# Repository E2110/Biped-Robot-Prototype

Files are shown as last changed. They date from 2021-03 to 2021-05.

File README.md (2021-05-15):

# Biped-Robot-Prototype

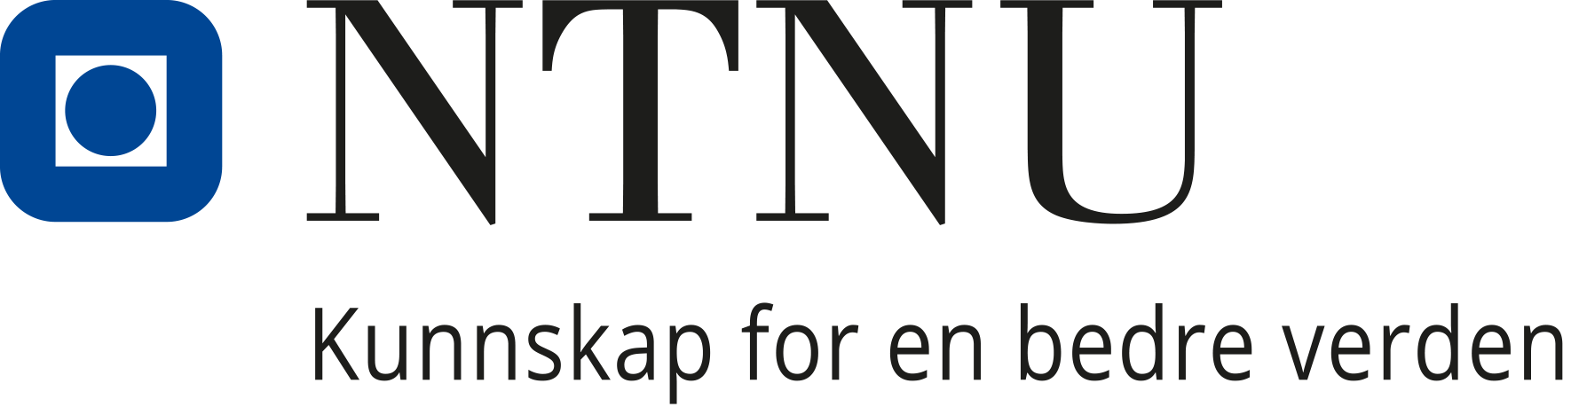
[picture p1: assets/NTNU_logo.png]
NTNU_logo


This is the reposatory for our Bachelor's thesis. The target group for this git is other electrical engeneering students at NTNU. Therefor knowledge acquired during the course of study is to be expected. The documentaions and explanaitons in this git should give enough information to be a foundation for further work. 

Anyways this project is about a thin and simple robot that can't walk. We will teach it to walk. How? Through C++ and ROS. Each part of the robot will have it's own floder where we explain the code and everything? associated with that part. 

https://user-images.githubusercontent.com/78819338/118373048-e83d3c00-b5b4-11eb-93af-3f74fb1a81d0.mp4

# Flashing Ubuntu 18.04
From windows OS. For flashing the new image we used following:

* Micro-SD, 16 GB
* 7-zip
* balenaEtcher

1 . Download prebuilt image from https://elinux.org/BeagleBoardUbuntu. As of writing the direct link to the image is https://rcn-ee.com/rootfs/2020-03-12/flasher/bone-eMMC-flasher-ubuntu-18.04.4-console-armhf-2020-03-12-2gb.img.xz and the downloaded file is called.

```
 bone-eMMC-flasher-ubuntu-18.04.4-console-armhf-2020-03-12-2gb.img.xz
```
2. Extract the file using 7-zip. This will remove the .xz at the end of the file.

3. Insert the Micro-SD into the computer. Open balenaEtcher, select flash from file and pick the the newly extracted .img file. Select the Micro-SD as target. FLASH!

4. Remove the Micro-SD from computer and insert it into the Beaglebone.

5. Hold the S3-botton down while powering up the Beaglebone. Hold until the four lights left of the ethernet input lights up at the same time, then let go of the button. The Beaglebone will then boot for quite some time until its done.

# Connect to the BeagleBone through SSH.

```
ssh ubuntu@192.168.7.2
```
passord: temppwd

# Enable the PWM-pins
This depends on your device tree overlay. There are quite a bunch out there, this one follows the one we got from the flashed image above.

1. Change to root user.

```
sudo su
```
2. Go to the ocp folder for the pin you want use. In this example P9_16.

```
cd /sys/devices/platform/ocp/ocp:P9_16_pinmux
```

3. Use cat state to see what pin-mode is currently in use. Use echo to change to PWM.

```
echo pwm > state
```

# Write to the PWM-pins with terminal

After changing the state to PWM you can change the different PWM-values in /sys/class/pwm/-folder. This is done by echoing different values to the parameters you want to change. In the example under we do this to pin P9.14

```
cd /sys/class/pwm/pwm-4:0
```
The three parameters we care about:
* enable: Turn on and of the pin.
* period: Decides the frequency. 
* duty_cycle: Time high during the period. If you put it the same as the period it will be constant high.

```
echo 1000000 > period
echo 200000 > duty_cycle
echo 1 > enable
```

# Write to the GPIO-pins with terminal
Go to the GPIO-folder
```
cd /sys/class/gpio
```
With the current Device Three Overlay the ls commando will show us a lot of gpio-pins to begin with. Even though only the current exported gpios should show up, we noticed that a lot of the pins were not exported. So if you can't change the paramters of a certain pin, we recommend trying to unexport and export that pin. This is done by echoing the number of the gpio to the unexport and export.

```
echo 114 > unexport
echo 114 > unexport
```
Now cd into the gpio you want to change.

```
cd gpio115
```
The two paramteres you should care about:
* direction: either in or out
* value: 1 or 0

# Install ROS-melodic

http://wiki.ros.org/melodic/Installation/Ubuntu

# Transfering files to the BeagleBone
## Linux
To do this we use scp command in the terminal

```
scp localfile.cpp ubuntu@192.168.7.2:/folder
```
Eclipse is also a common tool you can use for this and cross compiling.

## Windows
To transfer from windows we use WinSCP. Its pretty straight forward to use, kind of like a windows version of eclipse. 

1. Go to https://winscp.net/eng/download.php and install Winscp.

2. Connect the Beaglebone to your computer and open Winscp. This should pop up.

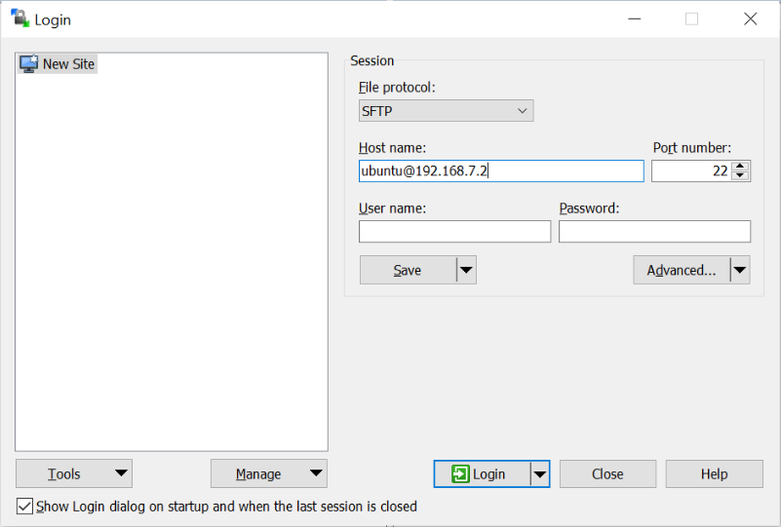
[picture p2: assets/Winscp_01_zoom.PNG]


3.Write ubuntu@192.168.7.2 into Host name. Port Number should stay at 22.

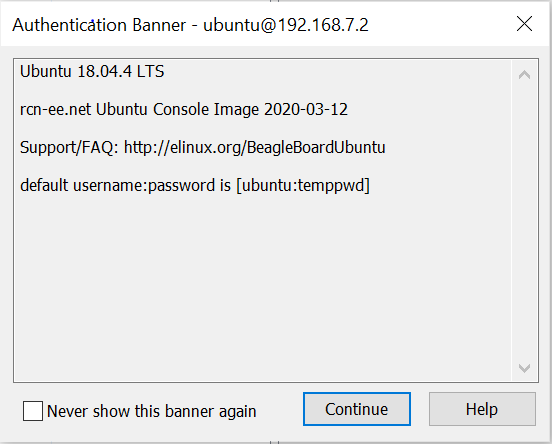
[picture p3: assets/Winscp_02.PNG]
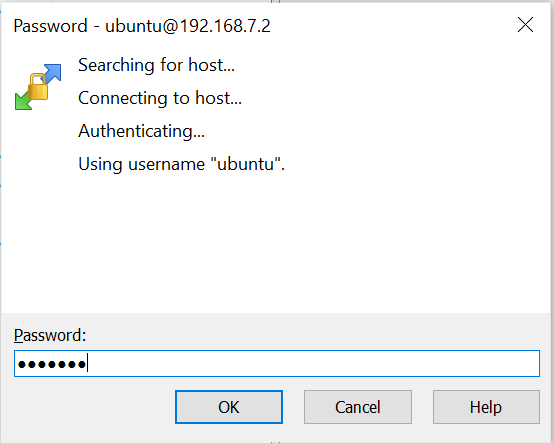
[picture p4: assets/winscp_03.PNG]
|

4. When connected you can easily drag end drop between the Beaglebone and the pc. You can also edit the different files on beaglebone.

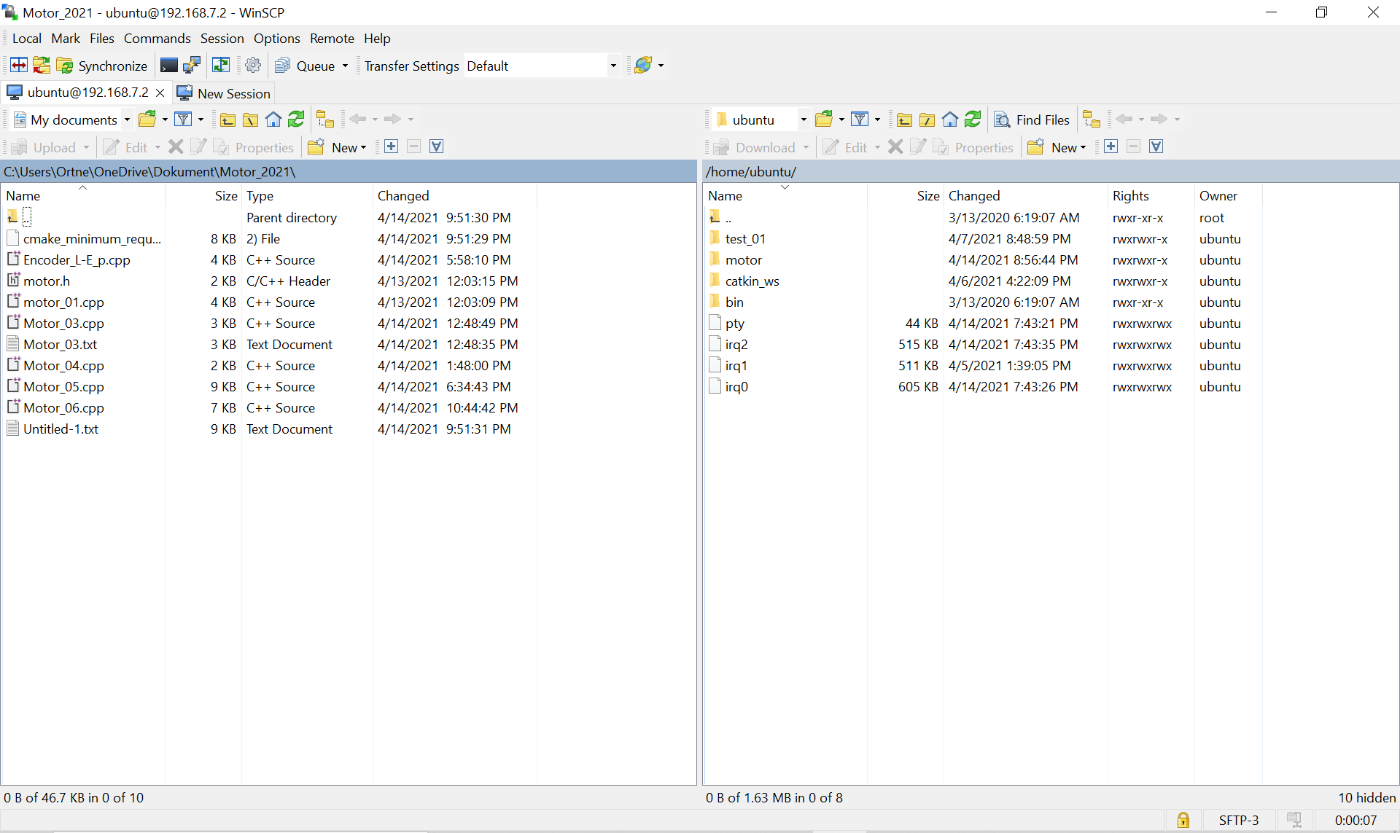
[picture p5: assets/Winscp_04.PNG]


# Make a Catkin-workspace, compile and run a C++-file with ROS
<i> This should be failry simple if you have gone through the ROS-tutorials. We'll keep it as short as possible.</i> 

1. Open one terminal (Ctrl + Alt + T) and run roscore

```
roscore
```
2. Open another (Ctrl + Shift + T) and source setup.bash

```
source /opt/ros/melodic/setup.bash
```
3. Make a folder and another named "src" within this one.

```
mkdir folder_01
cd folder_01
mkdir src
```
4. Make Cmakelists.txt vha. catkin_init_workspace

```
cd src
catkin_init_workspace
```
5. Exit src and run catkin_make

```
cd ..
catkin_make
```
6. source setup.bash

```
source devel/setup.bash
```

7. Make package

```
cd src
catkin_create_pkg folder_02 roscpp std_msgs
```
8. Import C++-file to new src folder.
9. To be able to run a C++-file you have to edit CMakelists.txt in folder_02

```
nano CMakeLists.txt
```
Under "Build"-section you can uncomment the "add_executable", "add_dependencies" and "target_link_libraries". Optionally just add:

```
add_executable(number_3 src/C++-file.cpp)
add_dependencies(number_3 ${${PROJECT_NAME}_EXPORTED_TARGETS} ${catkin_EXPORTED_TARGETS})
target_link_libraries(number_3 ${catkin_LIBRARIES})
```
10. Go to folder_01 and run catkin_make. This should compile the package.
```
cd ../..
catkin_make
```
11.Run the package
```
rosrun number_3 folder_02
```

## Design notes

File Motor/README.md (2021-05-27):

# Motor

The motors are located at the joint between torso and legs. By manipulating the ratio between period and duty-cycle we can decied the current delivered to the motors and by changing the value of the GPIO-pins we can change the directions of the motors. In the robots embeded system this part consists of three parts:

Maxon Motor 14887            |   ESCON 70/10 Servocontroller    |   Gearhead GP42C
:------------------------------------:|:-------------------------------------:|:-------------------------:
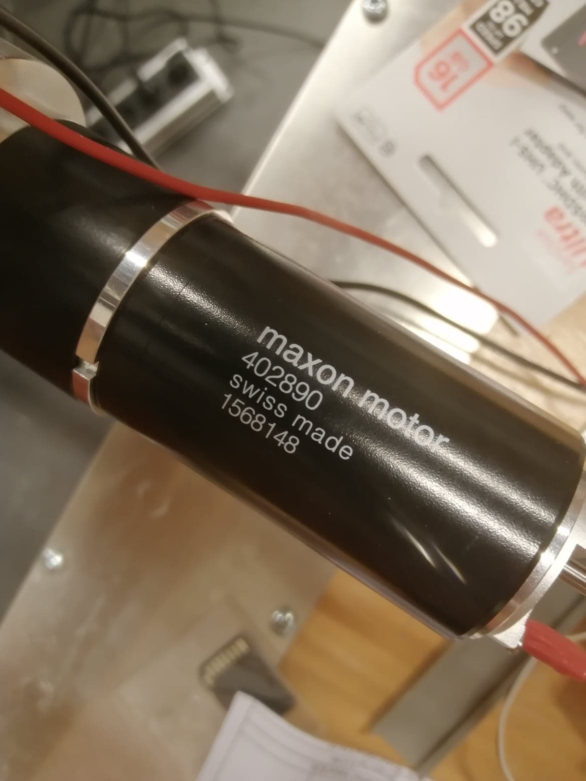
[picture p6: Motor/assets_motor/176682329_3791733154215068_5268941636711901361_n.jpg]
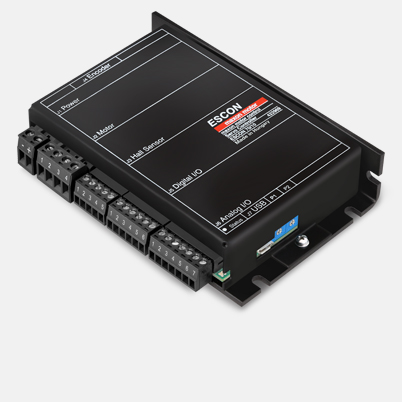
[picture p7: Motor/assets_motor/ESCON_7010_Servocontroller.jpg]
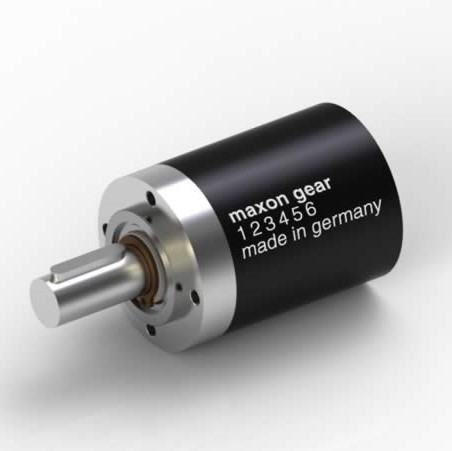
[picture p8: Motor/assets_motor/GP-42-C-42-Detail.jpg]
  |   | 

NB. The part number written on the motor (402890) is the part number for the particular motor/gearhead combination. We also have a spare with the number 241318. This consists of the same motor, but different gearhead. The spare gearhead has a ratio of 1:26.

The implemented gearheads have ratios of 1:6. 

Before the code for the motor is run its important to configure the servo controller with the ESCON studio software. Work done by a prior bachelor thesis group determined that the maximum required amperage for the motor should be 8.3A, this should be configured with the ESCON software including preforming a autotuning.

## Configure the servo-controller
To configure the ESCON 70/10 Servocontroller you need:
* Escon studio (Software)
* Micro USB
* Power Supply (If you want to Auto tune it)
The config is quite simple. Just start the software and (if connected) a pop up for configuration of ESCON 70/10 will pop up. The pictures under shows what we did step for step.

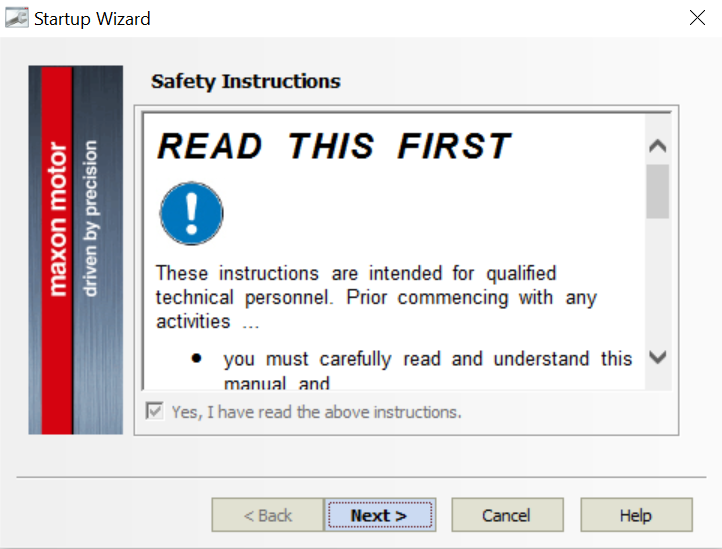
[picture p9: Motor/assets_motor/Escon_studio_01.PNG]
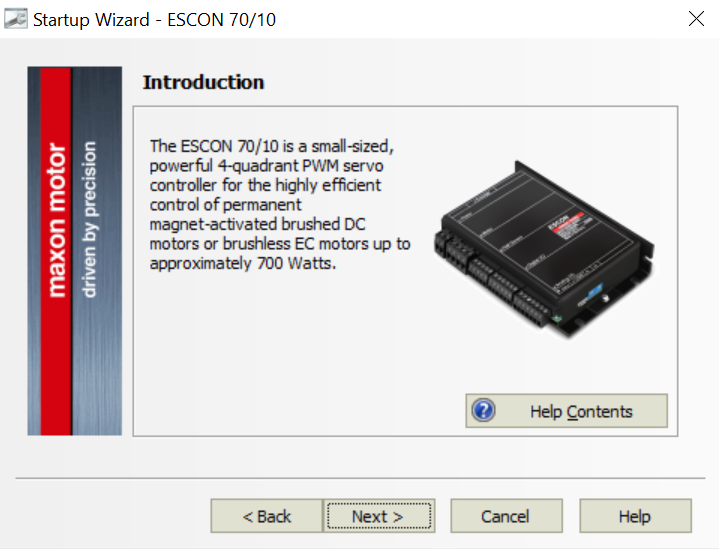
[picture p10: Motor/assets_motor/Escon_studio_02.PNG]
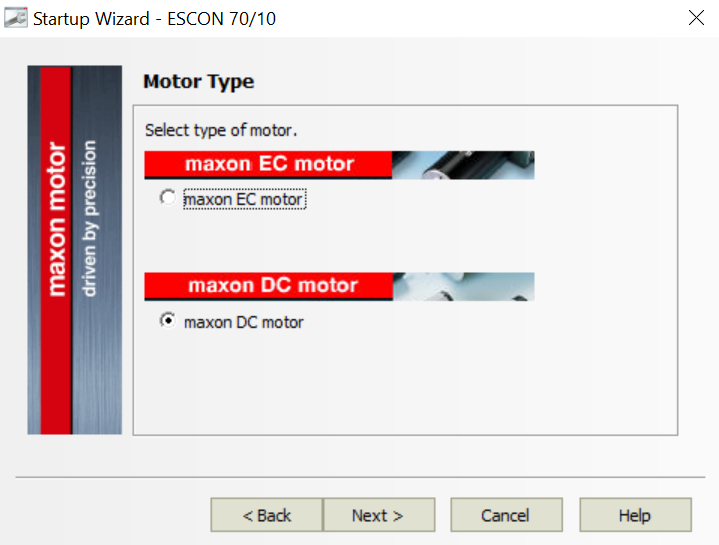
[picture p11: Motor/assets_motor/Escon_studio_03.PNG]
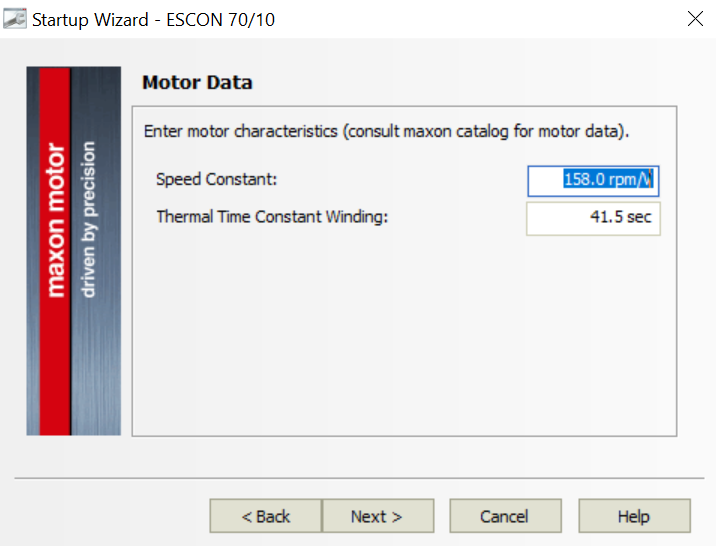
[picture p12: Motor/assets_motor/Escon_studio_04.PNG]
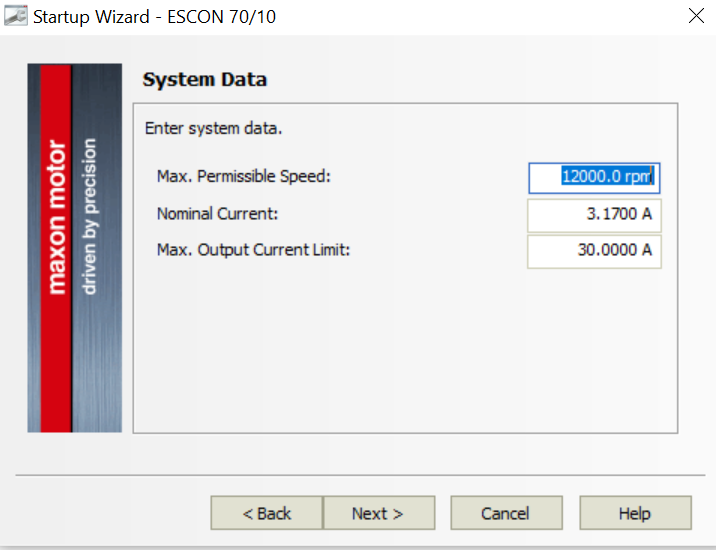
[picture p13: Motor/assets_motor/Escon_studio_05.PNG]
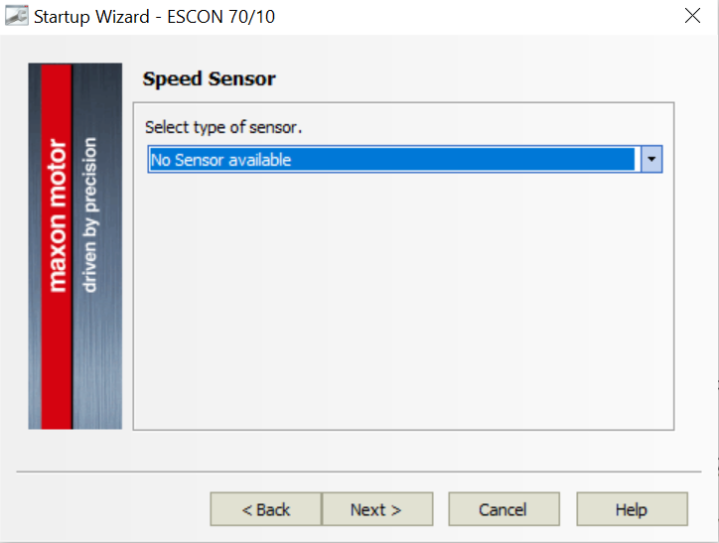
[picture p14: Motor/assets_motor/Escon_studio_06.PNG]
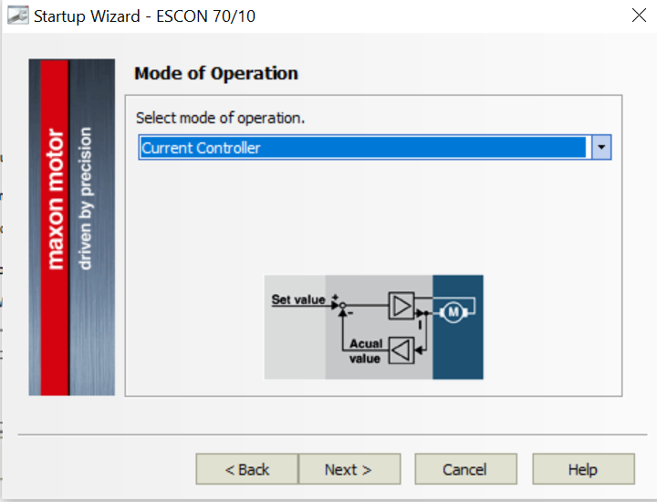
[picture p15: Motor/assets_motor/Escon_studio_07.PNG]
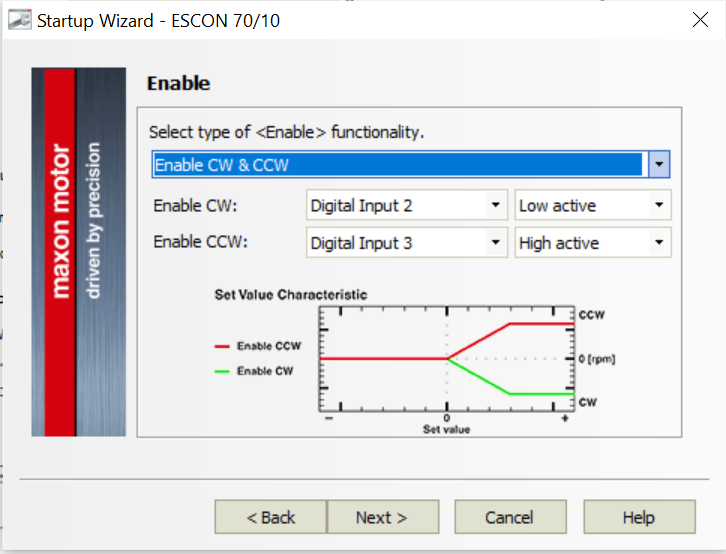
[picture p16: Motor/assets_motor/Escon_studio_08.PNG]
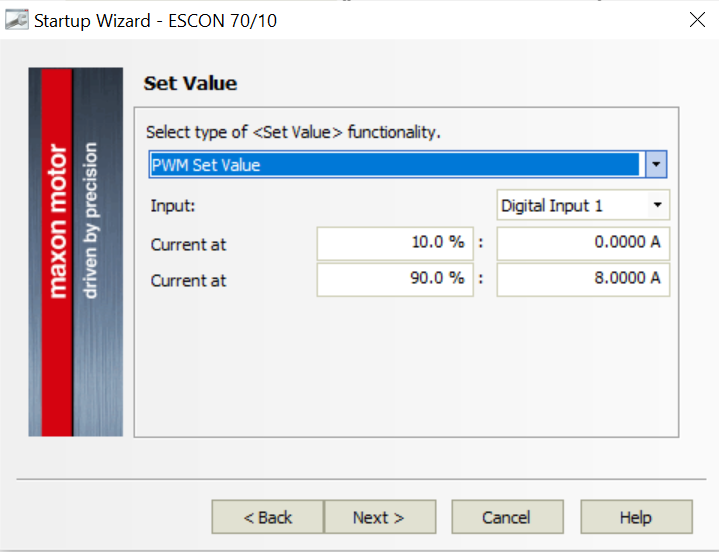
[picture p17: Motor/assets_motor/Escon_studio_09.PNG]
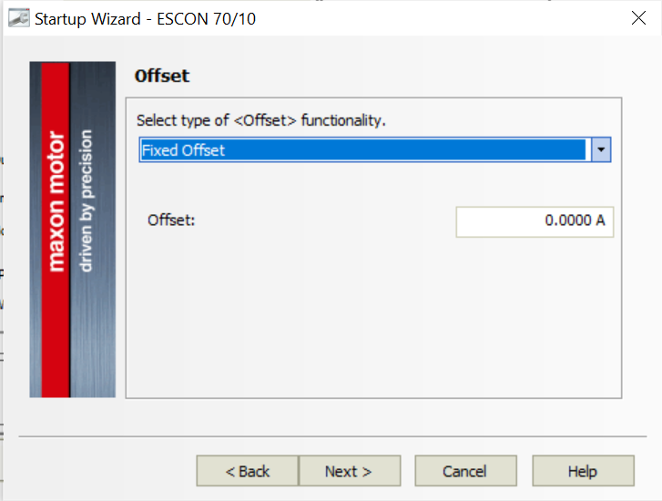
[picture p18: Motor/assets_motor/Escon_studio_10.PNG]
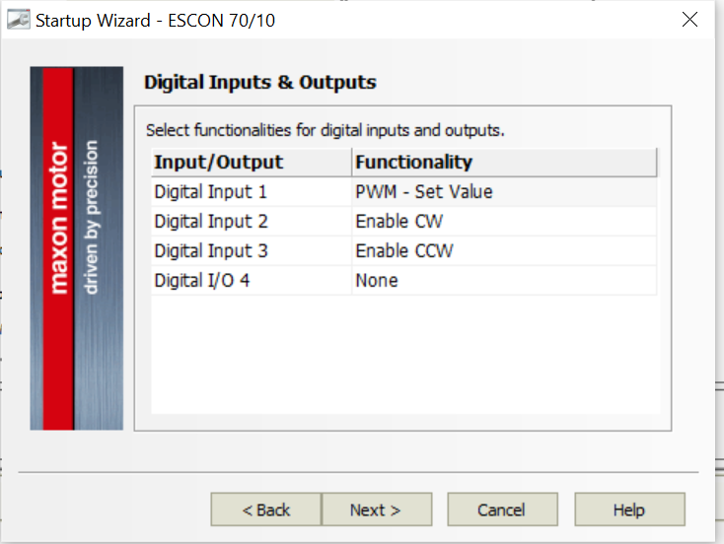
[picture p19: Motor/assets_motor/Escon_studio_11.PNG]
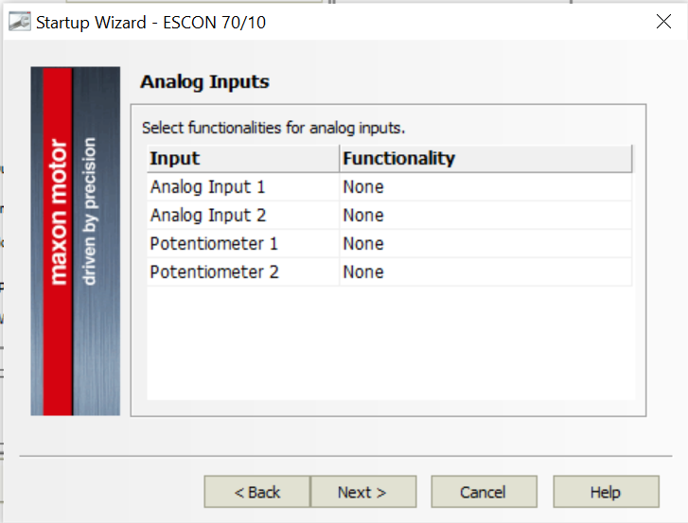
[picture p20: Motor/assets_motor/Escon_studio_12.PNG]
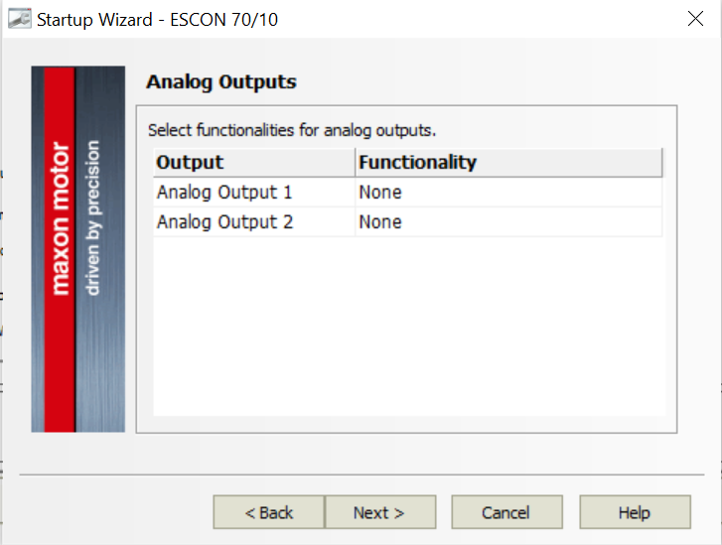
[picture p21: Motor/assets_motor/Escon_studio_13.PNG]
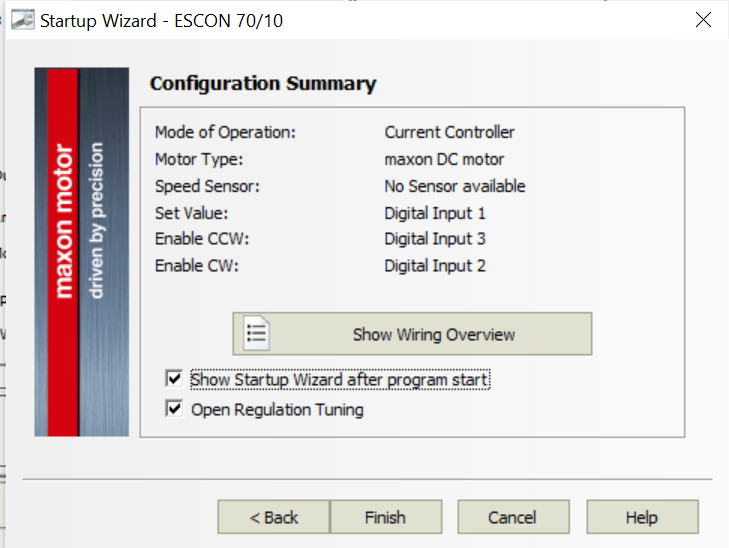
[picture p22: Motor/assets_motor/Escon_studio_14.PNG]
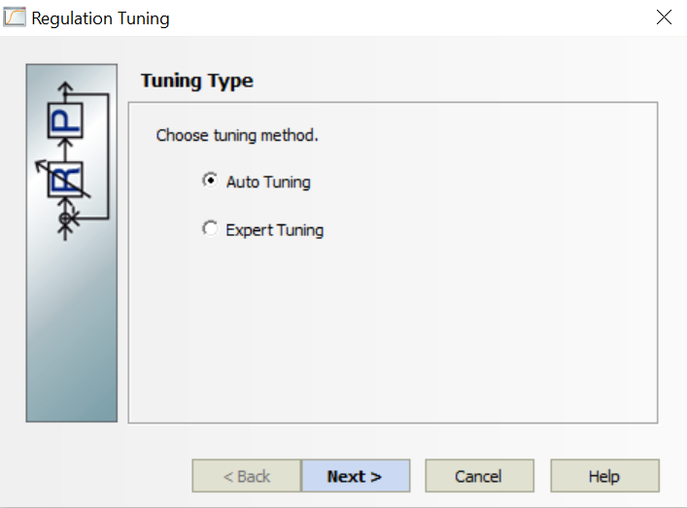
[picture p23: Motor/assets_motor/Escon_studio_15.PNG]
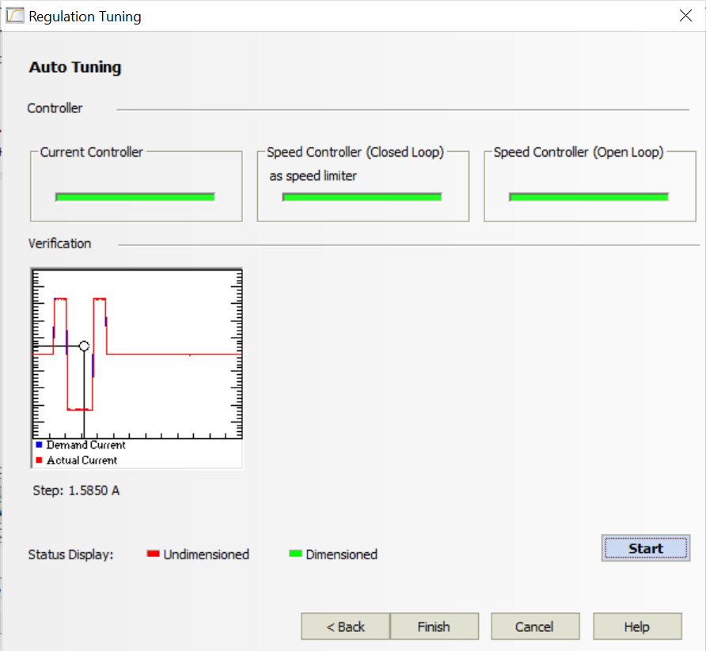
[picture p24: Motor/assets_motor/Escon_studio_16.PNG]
|||||||||||||||

## Connection and pins
Each motor is controlled by two by two GPIO-pins and one PWM-pin.

Pin     |   Inner Leg     | Outer Leg |  Servo Controller
:------------------------------------:|:-------------------------------------:|:-------------------------:|:--------:
GPIO 1  |   P9_23           |  P9_27 |J5_1
GPIO 2  |   P9_25           |  P8_34 |J5_2
PWM     |   P9_16           |  P9_14 |J5_3

Ground  |   Current     |   Motor - |   Motor   +
:---------:|:------:|:-----:|:------:
J1_-    |   J1_+    |   J2_1    |   J2_2
## Code
<i>This section will only explain the motor part, even though the code contains an encoder part. The explanation should give you enough information to understand the code, add new PWM- and GPIO-pins and change the values written on the Beaglebone, hopefully without having experience with C++. Order: Code -> where it's called -> explanation.

The code is written in C++. The purpose of the code is to change the direction and the torque of both motors. To control the direction you change the "value" of the GPIO-pins and to manipulate the torque you change the "duty_cycle" of the pwm-pins. Let's start with class motor.

* <b>class motor</b> contains functions with pathways to different folders on the Beaglebone. These pathways might be wrong if you do not have the same device tree overlay as us. 

```
    motor(int pinNumber)
    {
        m_dutyCycle = 1000000;
        setpwmPin (pinNumber);
        std::cout<< "Running with pin " << pinNumber << std::ends;
    }
```
pinNumber input:
```
motor control(14);
motor control2(16);
```
It starts by calling the setpwmPin function and printing what pinNumber it runs with. This equals the motor input and will decide which pwm-pin that will run.

```
void setDutyCycle(int dutyC)
    {
        std::ofstream DCfile;
        DCfile.open("/sys/class/pwm/pwm-" + m_PinpathNumber + "/duty_cycle");
        DCfile << dutyC;
        DCfile.close();
    }
```
initiated:
```
control.setDutyCycle(5000000);
control2.setDutyCycle(5000000);
```
When initiated it opens the duty_cycle folder, writes the input and closes it. m_PinpathNumber is given in the setpwmPin-function.

```
void setPWMfreq(int frequency)
        {
            disablePWM();
            std::ofstream freqSet;
            freqSet.open("/sys/class/pwm/pwm-" + m_PinpathNumber + "/period");
            freqSet << frequency;
            freqSet.close();
            enablePWM();
        }
```
Same concept as last function. Difference is that it calls a function to disable and enable the PWM-pin. The reason for this is that you can't change the period when the PWM-pin is enabled.

```
void GPIOtoggle(int cape_nr,int pin_nr,int state)
    {   
        setGPIOpin(cape_nr,pin_nr);
        setGPIOstate();
        setGPIOdirection("out");

        std::ofstream pinstream;
        pinstream.open("/sys/class/gpio/gpio"+ m_GPIONumber + "/value");
        pinstream << state;
        pinstream.close();
    }
```
It first calles tree functions to select the correct pin and put the direction "out" (default it's in". This function is used to put the GPIO value to either 1 or 0. Under section <i>"Connection and pins"</i> it is explained what the different combinations will do to the motor. 

```
    void motorInit()
    {   
        setPWMstate();
        exportPWM();
        setPWMfreq(m_frequency);
        setDutyCycle(m_dutyCycle);
        enablePWM();  
    }
```

motorInit is, as the name indicates, an initialiser. It calls function to make sure the PWM-pins are correct set up.

* main() will run when initiating the program.
* motor control(14); and motor control(16); calls different motors

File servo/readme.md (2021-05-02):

# Servo

As of 2021 four Turnigy TGY-SC340V 6.0-7.4 Volt servos are used to actuate the "toes" at the end of the robot legs. To control the servos two PWM signals is used. Each signal control one set of actuators on each leg. Beaglebone comes with plenty of PWM pins, pin P8 13 and P8 19 were selected to be used for the PWM signals for servo control.

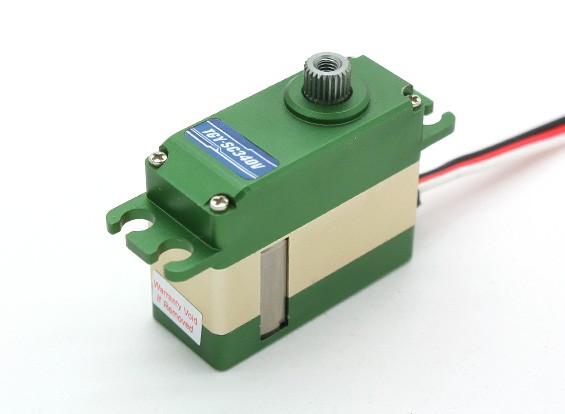
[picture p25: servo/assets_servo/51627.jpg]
Turnigy


## Servo Code

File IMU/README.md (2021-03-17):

# IMU

The inertial measurement unit used in the embedded system of the bipedal robot is the LSM9DS1 iNEMO system-in-package module developed by STMicroelectronics, this module has the ability to sense a total of 9 degrees of freedom (3-axis accelerometer, 3-axis gyroscope, and 3-axis magnetometer) and includes support for both SPI and I2C for communication. 

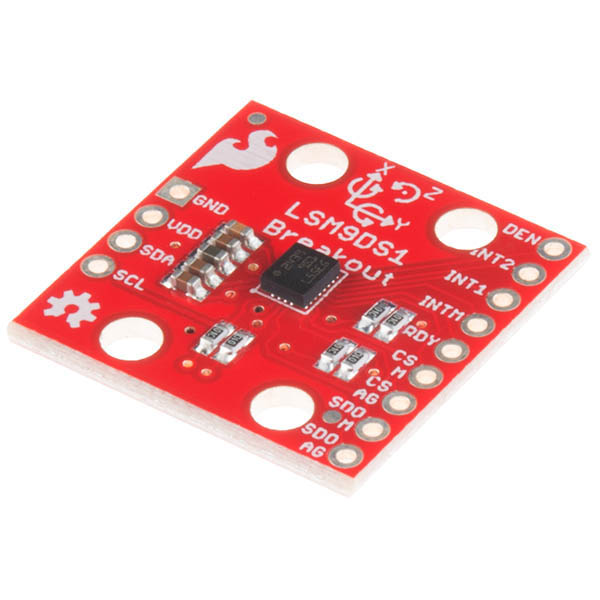
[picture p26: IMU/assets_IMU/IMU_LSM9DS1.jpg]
IMU_picture


The IMU are implemented on the robot with a breakout board for the LSM9DS1 chip produced by Sparkfun, this simplifies the process of connection to the pinouts of the chip and the interfacing with the IMU connector board which pass the data through ethernet cables to the Beaglebone.

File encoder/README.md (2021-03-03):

# Encoder

The encoder used in this project is a Scancon 2RMHF industrial encoder that outputs two square wave pulse signals, 3000 times per revolution. To read these signals, the eQEP modules on the Beaglebone are used. The eQEP module reads the two pulses from the encoder and transform this into a number that increases 12000 times per revolution. This number is then stored in memory and is accessible through the interface file “/position” in the “sys/devices/platform/ocp/...” file system.

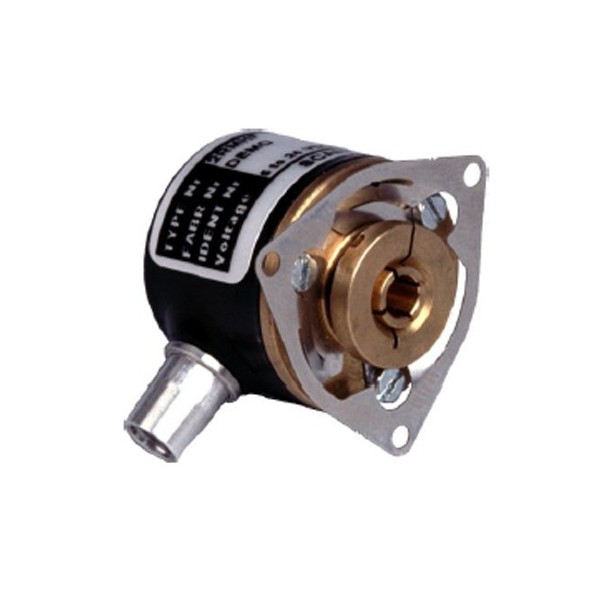
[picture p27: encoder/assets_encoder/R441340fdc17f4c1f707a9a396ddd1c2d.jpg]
Encoder


Encoders on the robot uses separate eQEP pins on the Beaglebone, so each encoder gets its own interface file in their own folder in the /ocp file system

## Code explanation

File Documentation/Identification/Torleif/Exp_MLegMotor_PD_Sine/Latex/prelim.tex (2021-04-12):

\documentclass[12pt]{article}

\usepackage{amsmath}
\usepackage{graphicx}
\usepackage{epstopdf}

\begin{document}

\section{Introduction}

\section{Method}

The pendulum is set to follow an angular reference given as a sinusoid 
\begin{equation}
\theta^* = A\sin(2\pi f t + \varphi),
\end{equation}
where the tracking is achieved by a PD - controller, giving the closed-loop system
\begin{equation}
\ddot{\theta} + \zeta\omega_0\dot{\theta} + \omega_0^2\theta = \frac{K_m}{I_f}\left[K_p(\theta^*-\theta) + K_d(\dot{\theta}^*-\dot{\theta})\right]
\end{equation}
where
\begin{equation}
\omega_0 = \sqrt{\frac{m_fgl_f}{I_f}}
\end{equation}
is the undamped resonance frequency, $\zeta$ is a friction term and $K_m$ is the assumed constant gain of the motor. Rearranging the equation gives
\begin{equation}
\ddot{\theta} + \left(\zeta\omega_0 + \frac{K_mK_d}{I_f}\right)\dot{\theta} + \left(\frac{m_fgl_f+K_mK_p}{I_f}\right)\theta = \frac{K_m}{I_f}\left[K_p\theta^*+ K_d\dot{\theta}^*\right]
\end{equation}
where the resonance frequency is now a function of the proportional control term $K_p$ and motor gain $K_m$
\begin{equation}
\omega_{K_P}^2 = \left(\omega_0^2 + \frac{K_mK_p}{I_f}\right) = \left(\frac{m_fgl_f+K_mK_p}{I_f}\right)
\end{equation}
The physical parameters of the pendulum can be further manipulated by attaching weights to each of the legs at fixed known distances from the center of rotation. These weights contributes at torque and moment of inertia according to their attachment point. 
\begin{equation}
\begin{split}
I_w = J_w + (m_w + m_f)(l_s + l_h/2 + (n_w-1)l_h)^2 \\
\tau_w = (m_w + m_f)g(l_s + l_h/2 + (n_w-1)l_h)
\end{split}
\end{equation}
where $n_w \in [0,8]$ is the mounting hole, $l_s$ is the distance to the first mounting hole, $l_h$ is the distance between mounting holes, $m_w$ and $m_f$ is the mass of the weights and fixtures, and $J_w$ is the moment of inertia around the weights center of gravity. The resonance frequency can then be adjusted as 

\begin{equation}
\omega_{K_P}^2  = \left(\frac{m_fgl_f+\tau_w+K_mK_p}{I_f + I_w}\right)
\label{eq:w0kp}
\end{equation}
where $I_w=\tau_w = 0$ if $n_w = 0$. 

Multiple experiments where then carried out with different $K_p$ and $n_w$, and each experiment was ran 3 times to increase statistical significance
\begin{table}
\caption{Table of experiments}
\label{tab:exp}
\begin{center}
\begin{tabular}{c|c|c|c|c|c|c|c|c}
$n_w$ / $K_p$ & 6 & 7 & 8 & 9 & 10 & 11 & 12 & 15 \\ \hline 
(0,0) &   & x & x & x & x & x & x & x\\
(1,1) &   &   & x &   &   &   &   &  \\
(8,8) &   &   & x & x & x &   &   &  \\
(5,5) &   &   & x & x & x &   &   &  \\
(2,8) &   &   & x & x & x &   &   &  \\
(3,7) & x &   & x & x & x &   & x &  \\
(1,0) &   &   & x &   &   &   &   &  \\
(4,0) &   &   & x &   &   &   &   &  \\
(7,0) &   &   & x &   &   &   &   &  
\end{tabular}
\end{center}
\end{table}
The experiments that were performed with $\geq 3$ different $K_p$ values were used to estimate the motor gain $K_m$ by treating $\omega_{K_p}^2$ as a linear function
\begin{equation}
\begin{split}
\omega_{K_P}^2  &= \left(\frac{m_fgl_f+\tau_w+K_mK_p}{I_f + I_w}\right)\\
 y &= ax + b \\
 a = \frac{K_m}{I_f+I_w}, \quad x = K_p, \quad y &= \omega_{K_P}^2, \quad b = \left(\frac{m_fgl_f+\tau_w}{I_f + I_w}\right)
\end{split}
\end{equation}
After obtaining the lumped expression for $\frac{K_m}{I_f+I_w}$, the remaining parameters $m_fgl_f$ and $I_f$ could be found by rearranging \eqref{eq:w0kp} as
\begin{equation}
\begin{split}
\omega_{K_P}^2  &= \left(\frac{m_fgl_f+\tau_w}{I_f + I_w} + aK_p\right)\\
\begin{bmatrix}
1 & -\omega_{K_P}^2 + aK_p 
\end{bmatrix}
\begin{bmatrix}
m_fgl_f \\
I_f
\end{bmatrix}
&=
\omega_{K_P}^2I_w-\tau_w-aK_pI_w 
\end{split}
\end{equation}
for each experiment in Table \ref{tab:exp}, and constructing an overdetermined set of equations on the form
\begin{equation}
Ax=b
\end{equation}
where $ x = [m_fgl_f, I_f]^T$, and the solution is given by least-squares fitting as
\begin{equation}
x = \left(A^TA\right)^{-1}b.
\end{equation}

\section{Results}

\begin{figure}[htbp]

\label{fig:km_00}
\caption{Estimated linear fit for $\frac{K_m}{I_f+I_w}$ parameter for experiments without weights attached.}
\end{figure}

\begin{figure}[htbp]

\label{fig:km_55}
\caption{Estimated linear fit for $\frac{K_m}{I_f+I_w}$ parameter for experiments with weights attached at $n_w = (5,5)$.}
\end{figure}

\begin{figure}[htbp]

\label{fig:km_88}
\caption{Estimated linear fit for $\frac{K_m}{I_f+I_w}$ parameter for experiments with weights attached at $n_w = (8,8)$.}
\end{figure}

\begin{figure}[htbp]

\label{fig:km_28}
\caption{Estimated linear fit for $\frac{K_m}{I_f+I_w}$ parameter for experiments with weights attached at $n_w = (2,8)$.}
\end{figure}

\begin{figure}[htbp]

\label{fig:km_37}
\caption{Estimated linear fit for $\frac{K_m}{I_f+I_w}$ parameter for experiments with weights attached at $n_w = (3,7)$.}
\end{figure}

\begin{table}
\caption{Motor gain estimates}
\label{tab:km}
\begin{center}
\begin{tabular}{c|c}
$n_w$ & $\frac{K_m}{I_f+I_w}$ \\ \hline 
(0,0) &   0.424071985869166\\
(8,8) &  0.310548831022341 	\\
(5,5) & 0.425654308341756 \\
(2,8) & 0.374895472210993 \\
(3,7) & 0.303311751403483 \\
\end{tabular}
\end{center}
\end{table}

\begin{table}
\caption{Parameter estimates}
\label{tab:param}
\begin{center}
\begin{tabular}{c|c}
$m_fgl_f$  & 7.213988198586391\\
$I_f$ & 0.200275108832547\\
$K_m$ & 0.096860674406427\\
\end{tabular}
\end{center}
\end{table}

\begin{table}
\caption{Verification experiments}
\label{tab:km}
\begin{center}
\begin{tabular}{c|c|c|c}
$n_w$ & $\omega_0^*$ & $\omega_0$ & error \\ \hline 
(1,1) &      6.341697809300672 &   6.375158252674985 &  -0.033460443374313 \\
(1,0) &     6.297273096333526 	&   6.347945772068390 &  -0.050672675734864	\\
(4,0) &    6.182221951346674 &   6.221128813138584 &  -0.038906861791911\\
(7,0) &    6.022659862653705&   6.037844301505593 &	  -0.015184438851888
\end{tabular}
\end{center}
\end{table}

\section{Conclusion}

\end{document}

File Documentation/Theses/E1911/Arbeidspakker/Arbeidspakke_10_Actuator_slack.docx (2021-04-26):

Department of Engineering Cybernetics,
Automation Technology Programme

Course: TELE3001 Bachelor Thesis | | | | | | Date: 24.01.2019

Project: Instrumentation of bipedal robotprototype
Activity: Actuator slack | | | | | | Activity nr:09
Starting date: 23.04.2019 | | | End date: 23.05.2019
Dependency: Joint control | Past Activities: | | IMU calculation Microcontroller
| Following Activities:

Goal: Eliminate actuator slack impact

Description: Measure actuator angles with encoder while switching torque direction on the actuators. Decide if measurement errors while switching are considerable. If the slack has a meaningful impact, find a way to compensate for it.
Total Workload: 100 hours | | | Work distribution: Kristoffer Jakob Henrik Jonas Endre | 20 hours 20 hours 20 hours 20 hours 20 hours

Expenses:

Resources:

Hazards: Motor torque,Voltage
Project supervisor: Torleif Anstensrud Project team members: Jakob Karlsen Jonas Hjulstad Endre T.Ellingsen Henrik Baldishol Kristoffer Nordvik | | Mail: torleif.anstensrud@ntnu.no jakob-karlsen@outlook.com jonasbhjulstad@gmail.com endre.t.e@hotmail.com henrik.baldishol@gmail.com kristono@stud.ntnu.no | | | Tlf: 95808760 46676230 40523352 46672181 95300104 99117516

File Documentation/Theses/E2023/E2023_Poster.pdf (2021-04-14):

# Biped Robot Prototype - Embedded system integration with PID controller

## Martin Skårerverket

1

## , Jonas Brunsvik

1

## , Irfan Ljevo

1

### 1Norwegian University of Science and Technology, Trondheim, Norway

## Introduction

In modern industry robots capable of mimicking human behaviour are of great importance not just for industrial purposes but also for medical work. Each year standards and accomplishments in sector of robotics and embedded systems are improving faster than before. Therefore understanding of such systems is crucial for upcoming engineers.

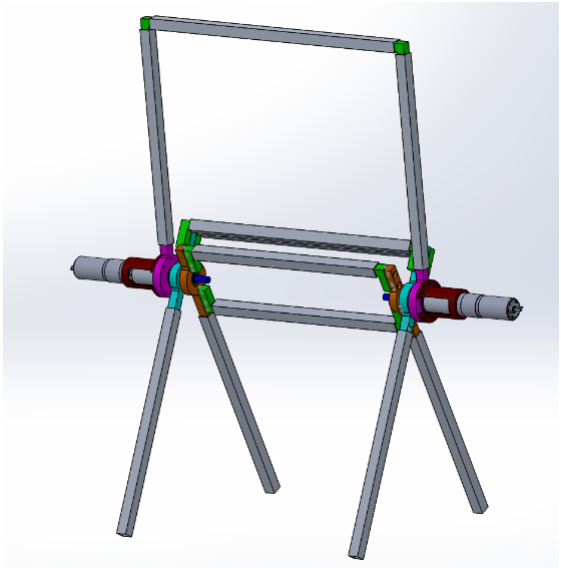
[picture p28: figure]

Figure 1: Prototype Biped robot Frame

Multiple master and bachelor thesis have been written on subject of biped gait robots at Norwegian University of Science and Technology (NTNU). This project aims to provide a development and test platform with the biped prototype at the department of engineering cybernetics at NTNU.

## Circuit Design

One of the main tasks the group had, when first trying to understand the wiring, and how everything was connected, was understanding the documentation. Much of the robots wiring system was built with unreliable solutions and with many protoboards in its design. To replace these protoboards the group decided to develop new PCB boards with connectors for each component. Since the previous work performed on robot had encountered issues with wiring and noise in the system, new wiring to each component would need to be developed. The new wiring scheme would be made in way that reduced the risk of connecting components the wrong way. This would hinder future work from accidentally damaging the Beaglebone or sensors connected. The focus of this new system of boards and wiring was to make it simple, easy to plug and play, and flexible enough for future changes to the robot.

New Wiring System

In order to create a more robust wiring system with ethernet cables, three custom connector PCBs was created. A main connector board, IMU connector board and an encoder connector board implements headers which makes it possible to use ethernet cables to connect the system components. The main connector board functions as a cape that connects to Beaglbones P8 and P9 headers. The focus of the design was to make it easy to connect and disconnect all the different components the robot uses. To achieve this the board uses Ethernet ports to connect to the IMUs and Encoders, and ordinary screw Terminals for the motor and Servo connections.To power the the Motor the board also splits 48 volts to two separate screw connectors for each motor controller. The IMU connector board help facilitate the LSM9DS1 breakout board and to connect the LSM9DS1 IMU chip through R-45 connectors and Ethernet cables to the main board. The encoder connector board interfaces the 10-pin connector from the encoder with the RJ45 header which transfers data through an Ethernet cable to the Beaglebone.

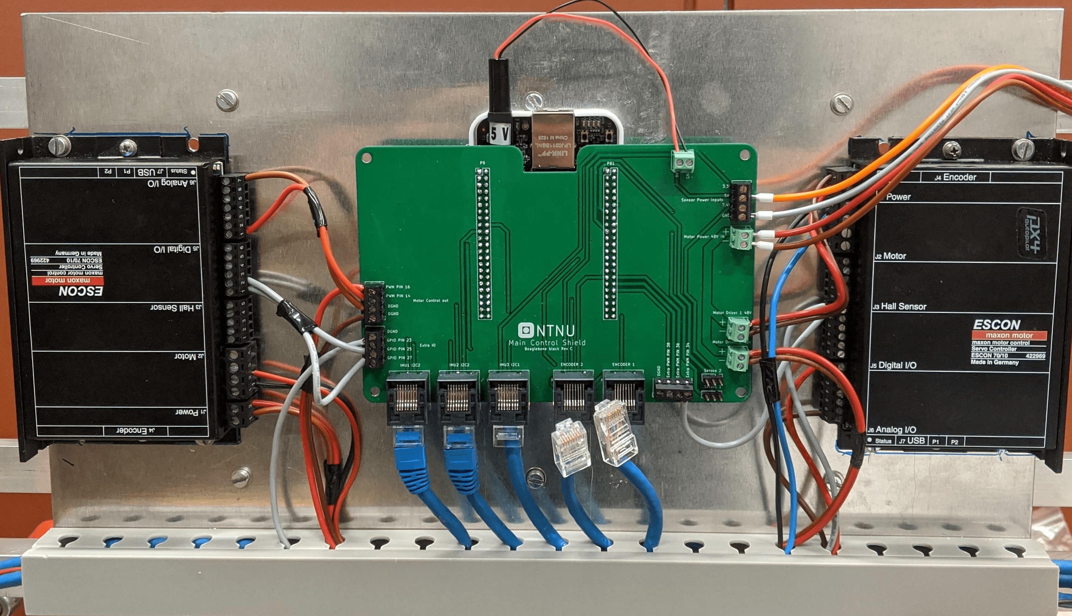
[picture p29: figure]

Figure 2: Main connector board

## Embedded system

The goal of the embedded system was to read all the sensors, and to control the motor and servos from the Beaglebone. This was to remove the costly dSpace ControlDesk from the project, and make it open source and easy to modify. Thorough documentation of the embedded development and code in GitHub repository was also an important goal of this project. It was decided to develop new code for all the sensors; servos and motors. Arduino used in the system were also removed since they represented an unnecessary complexity to the communication system between the Beaglebone and IMU. Since the code from the last group was written in Arduino C and in C++, and most of the members knew how to code in C, the new code was written in standard C++.

Beaglebone Black

The Beaglebone is the central processing unit of the embedded system of the biped robot. The Beaglebone Black is an open-source hardware System on Chip (SoC) development board made for intermediate level developers.

System Components

The inertial measurement unit used in the embedded system of the bipedal robot is the LSM9DS1 iNEMO systemin-package module developed by STMicroelectronics, this module has the ability to sense a total of 9 degrees of freedom, I2C was used for as the protocol for communication with the unit. The encoder used in this project is a Scancon 2RMHF industrial encoder that outputs two square wave pulse signals. Four Turnigy TGY-SC340V 7.4 Volt servos were used in the project to control the actuators at the end of the robot legs. The motor used in the embedded system of the robot are the Maxon 14887

DC motor which has the capability to output 150W, the motor is connected to a gearbox which gears the motor 1-to-6. The motor is controlled with the help of an ESCON 70/10 servocontroller.

ROS - Robot Operating System

The code developed for the system was with ROS implementation in mind because there are clear advantages for using ROS as the cross process communication framework, first it is easy to expand upon and very modular. Including additional sensor nodes or other servos and motors is easy to add, and is done quickly

## PD - controller

Determining a strategy on how system will be controlled and which controller to use, were based upon fact that robot is underactuated and underpowered. A system identification was performed, this involved modeling of the system with MATLAB and Simulink. Then it was determined to utilize a Proportional-Derivative controller for the control of the biped robot, the reasoning behind this decision was that the actuators found on the robot do not have the power needed to execute error correcting executions of the integral portion of an PID controller. In order to implement a PD-controller in the embedded system of the robot a discretization of the system, the method chosen to perform this was with trapezoidal approximation. This research was then used to create a C++ controller code which can be implemented on the embedded system of the biped robot.

## Summary and conclusions

The primary goal of this project was to develop a robust foundation for further development on this project. This meant having wiring that is simple enough for new students to understand, but also modular enough to not impede future changes. The group ended up with a new wiring system and fully functional C++ code for each sensor, servo, and motor. This code was short, easy to understand, and simple enough to perform further development. Documentation of the code in a GitHub repository will also aid the future development on the robot. The secondary goal of this project was to preform research into implementation of a PD – controller on the bipedal robot with the aim of the robot performing one or two steps. The research presents a suggestion for how the PD controller and how it could be implemented in ROS. In conclusion the current biped robot prototype has a functional embedded system with new modular wiring and the theoretical groundwork for the implementation of a PD controller for the robot is completed. The current system fulfills the main goals set for this project, but the group acknowledges that the limited testing of the physical system hinders the group to conclude that the control system of the robot is fully completed and ready for further development without modification uncovered by future testing.

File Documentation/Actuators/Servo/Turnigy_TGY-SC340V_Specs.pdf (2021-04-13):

13.04.2021

Servo specs

As of 2020 the Turnigy TGY-SC340V servos are used on the robot. We (E2110) have not been able to find a datasheet related to the servos, we have however been able to retrieve the following information from auction sites.


Manufacturers specifications
size :35mmx14mmx27mm (3 sheets eyes. image measurement) torque :2.8 kg.cm (6.0V)~3.6 kg.cm (7.4V)
Speed :0.05 sec/60deg (6.0V)~0.04 sec/60deg (7.4V)
voltage :6.0V ~ 7.4V
weight :33g
motor : core less
gear : metal
spline count :25
bearing : double ball race type : digital
plug :JR / Futaba

Sources:

https://page.auctions.yahoo.co.jp/jp/auction/b526191278

https://yahoo.aleado.com/lot?auctionID=b526191278

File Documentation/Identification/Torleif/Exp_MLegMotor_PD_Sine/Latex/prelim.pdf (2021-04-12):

## 1 Introduction

## 2 Method

The pendulum is set to follow an angular reference given as a sinusoid

θ

∗ = A sin(2πf t + ϕ), | (1)

where the tracking is achieved by a PD - controller, giving the closed-loop system
¨θ + ζω0

˙θ + ω
2/0 θ =

Km
If

h
Kp(θ

∗ − θ) + Kd(

˙θ

∗ − ˙θ)

i
(2)

where

ω0 =

s
mf glf
If

(3)

is the undamped resonance frequency, ζ is a friction term and Km is the assumed constant gain of the motor. Rearranging the equation gives

¨θ +

ζω0 +

KmKd
If
˙θ +
mf glf + KmKp
If
θ =

Km
If

h
Kpθ

∗ + Kd

˙θ
∗

i
(4)

where the resonance frequency is now a function of the proportional control term Kp and motor gain Km

ω

2
KP =
ω

2
0 +

KmKp
If
=
mf glf + KmKp
If
(5)

The physical parameters of the pendulum can be further manipulated by attaching weights to each of the legs at fixed known distances from the center of rotation. These weights contributes at torque and moment of inertia according to their attachment point.

Iw = Jw + (mw + mf )(ls + lh/2 + (nw − 1)lh)

2

τw = (mw + mf )g(ls + lh/2 + (nw − 1)lh)

(6)

where nw ∈ [0, 8] is the mounting hole, ls is the distance to the first mounting hole, lh is the distance between mounting holes, mw and mf is the mass of the weights and fixtures, and Jw is the moment of inertia around the weights center of gravity. The resonance frequency can then be adjusted as

1

Table 1: Table of experiments

nw / Kp | 6 | 7 | 8 | 9 | 10 | 11 | 12 | 15
(0,0) | | x | x | x | x | x | x | x
(1,1) | | | x
(8,8) | | | x | x | x
(5,5) | | | x | x | x
(2,8) | | | x | x | x
(3,7) | x | | x | x | x | | x
(1,0) | | | x
(4,0) | | | x
(7,0) | | | x

ω

2
KP =
mf glf + τw + KmKp
If + Iw
(7)

where Iw = τw = 0 if nw = 0.
Multiple experiments where then carried out with different Kp and nw, and each experiment was ran 3 times to increase statistical significance The experiments that were performed with ≥ 3 different Kp values were used to estimate the motor gain Km by treating ω

2
Kp

as a linear function

ω

2
KP =
mf glf + τw + KmKp
If + Iw

y = ax + b

a =

Km
If + Iw
, | x = Kp, | y = ω

2
KP

, b =

mf glf + τw
If + Iw

(8)

After obtaining the lumped expression for Km
If +Iw

, the remaining parameters mf glf and If could be found by rearranging (7) as

ω

2
KP =
mf glf + τw
If + Iw

+ aKp

1 −ω

2
KP + aKp

mf glf
If
= ω

2
KP

Iw − τw − aKpIw

(9)

2

for each experiment in Table 1, and constructing an overdetermined set of equations on the form
Ax = b | (10)

where x = [mf glf , If ]

T
, and the solution is given by least-squares fitting as

x =

A

TA

−1
b. (11)

## 3 Results

Estimates of ω; for different K; p Weight Pos 1: 0, Weight Pos 2: 0; average; run estimates

Figure 1: Estimated linear fit for Km
If +Iw

parameter for experiments without weights attached.

3

for different K; average; run estimates

Estimates of ω
Weight Pos 1: 5, Weight Pos 2: 5

Figure 2: Estimated linear fit for Km
weights attached at nw = (5, 5).

parameter for experiments with

Table 2: Motor gain estimates

Estimates of ω; for different K; p Weight Pos 1: 8, Weight Pos 2: 8; average; run estimates

Figure 3: Estimated linear fit for Km
If +Iw

parameter for experiments with weights attached at nw = (8, 8).

Table 3: Parameter estimates

mf glf | 7.213988198586391
If | 0.200275108832547
Km | 0.096860674406427

5

Estimates of ω; for different K; p Weight Pos 1: 2, Weight Pos 2: 8; average; run estimates

Figure 4: Estimated linear fit for Km
If +Iw

parameter for experiments with weights attached at nw = (2, 8).

Table 4: Verification experiments

nw | ω ∗
| 0 | ω0 | error
(1,1) | 6.341697809300672 | 6.375158252674985 | -0.033460443374313
(1,0) | 6.297273096333526 | 6.347945772068390 | -0.050672675734864
(4,0) | 6.182221951346674 | 6.221128813138584 | -0.038906861791911
(7,0) | 6.022659862653705 | 6.037844301505593 | -0.015184438851888

6

for different K; average; run estimates

Estimates of ω
Weight Pos 1: 3, Weight Pos 2: 7

Figure 5: Estimated linear fit for Km
weights attached at nw = (3, 7).

parameter for experiments with

## 4 Conclusion

8

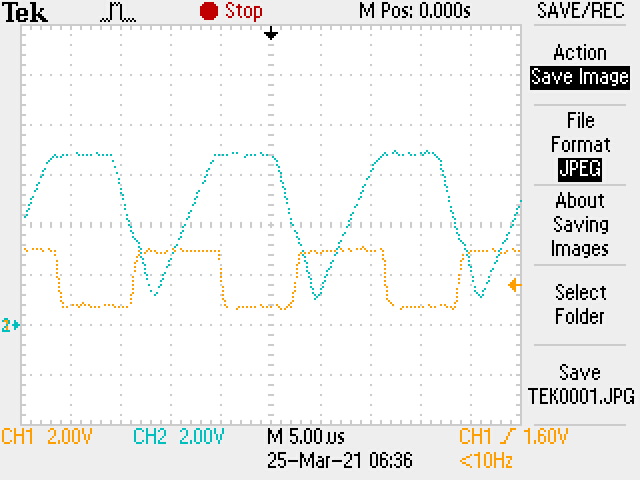
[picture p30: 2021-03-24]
Div/Images/TEK0001.JPG

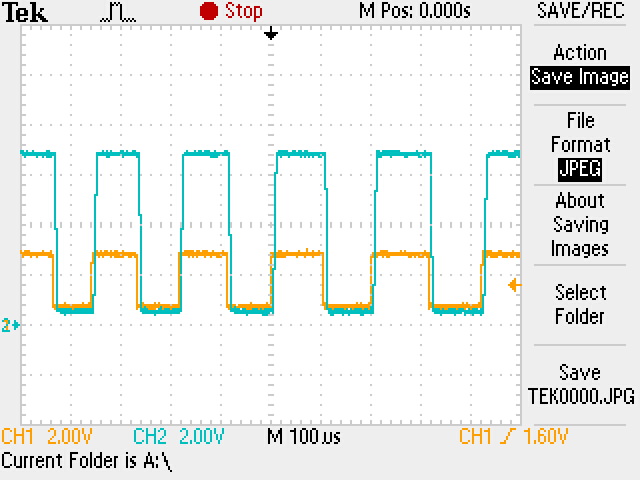
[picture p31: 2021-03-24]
Div/Images/TEK0000.JPG

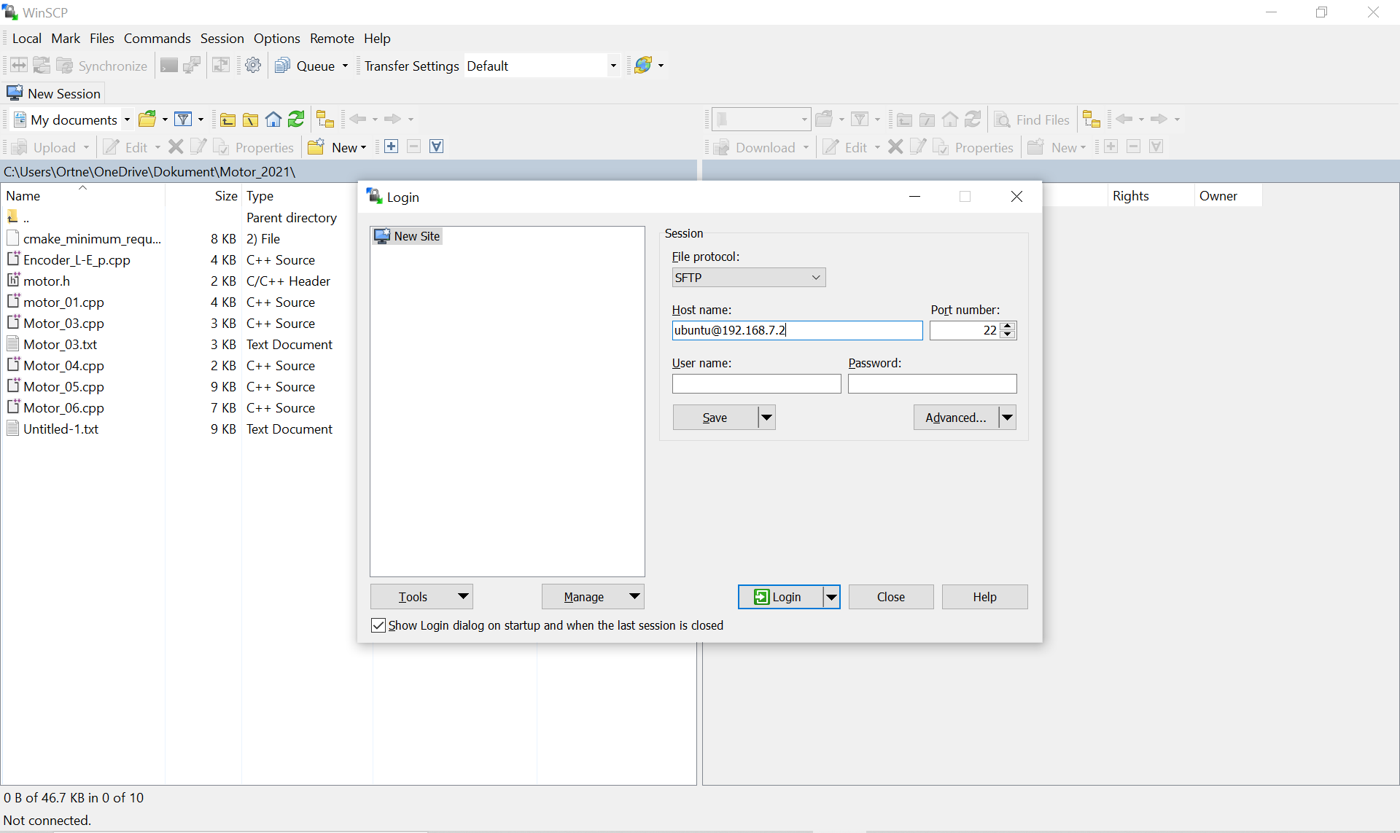
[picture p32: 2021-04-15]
assets/Winscp_01.PNG

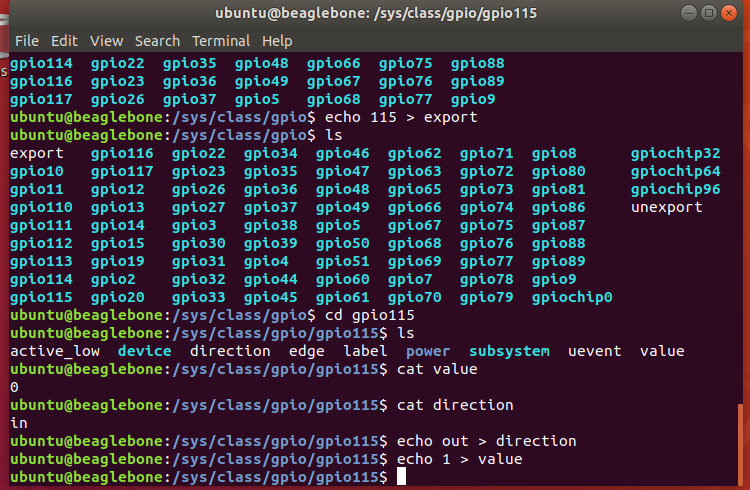
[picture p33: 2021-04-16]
Motor/assets_motor/Escon_studio_14.6.PNG

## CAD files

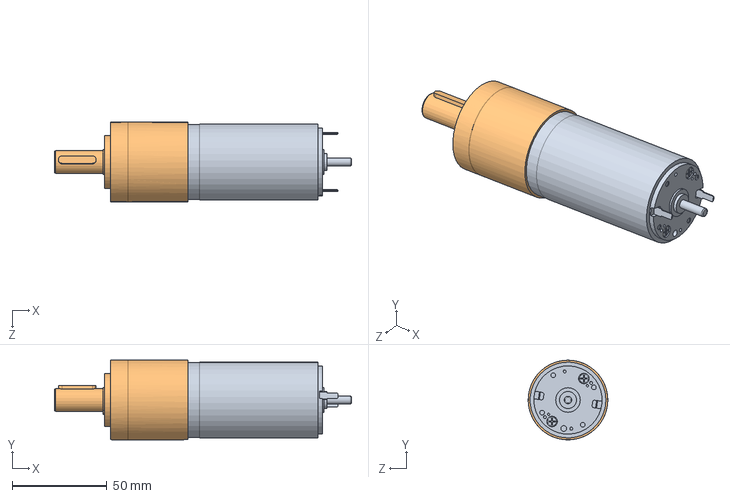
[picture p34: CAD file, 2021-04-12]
Documentation/CAD/12_082_stp/RE40_N6.SLDASM
156.6 x 42.0 x 42.0 mm
RE40
Gear_N6

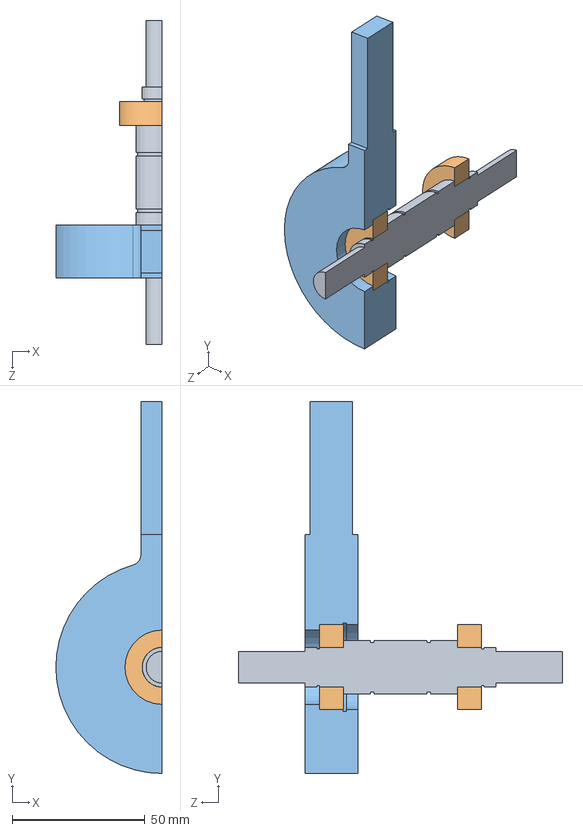
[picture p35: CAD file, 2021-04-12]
Documentation/CAD/Design_HIP20mm/Left_Hip.SLDASM
40.0 x 140.0 x 122.0 mm
Left_Axis
Bearing_ID15 x 2
Right_Hip_Body

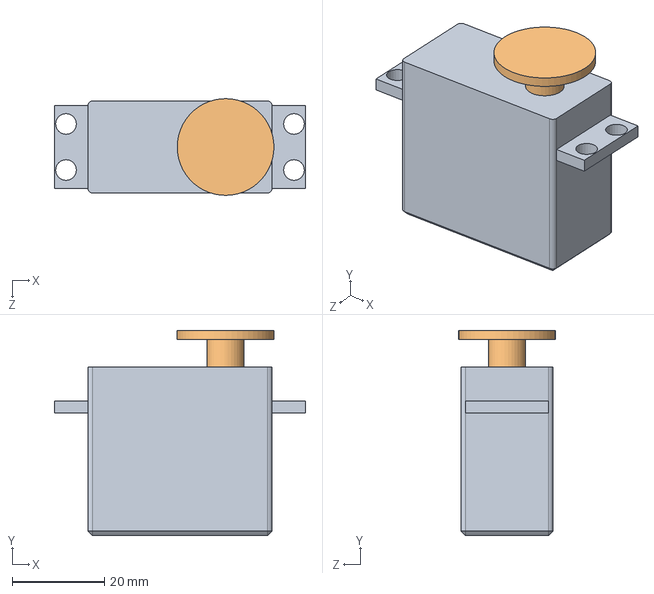
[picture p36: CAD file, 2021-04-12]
Documentation/CAD/Design_HIP16mm/Futaba_Servo_ASM.SLDASM
54.5 x 44.6 x 21.0 mm
Futaba_Servo
Futaba_Servo_Flange

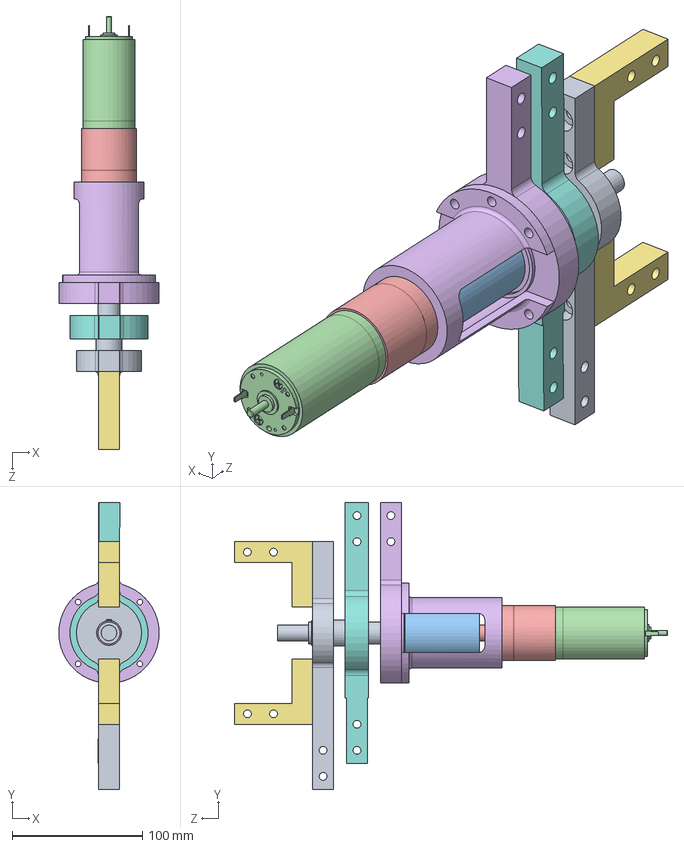
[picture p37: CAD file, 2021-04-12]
Documentation/CAD/Design_HIP16mm/Right_Hip.SLDASM
77.0 x 220.0 x 332.1 mm
Right_Axis
Bearing_ID15
Bearing_ID17
Ring_Shaft_15mm
Ring_Shaft_17mm x 2
Hip_Body
Ring_Bore_32mm
Right_Hip_MLeg
Right_Hip_ILeg
Ring_Bore_35mm
Coupling_12x12mm
RE40
Gear_N6
Motor_Shaft_Casing
ILeg_Profile_Fixture x 2
Feather_Key_4_4_15_mm

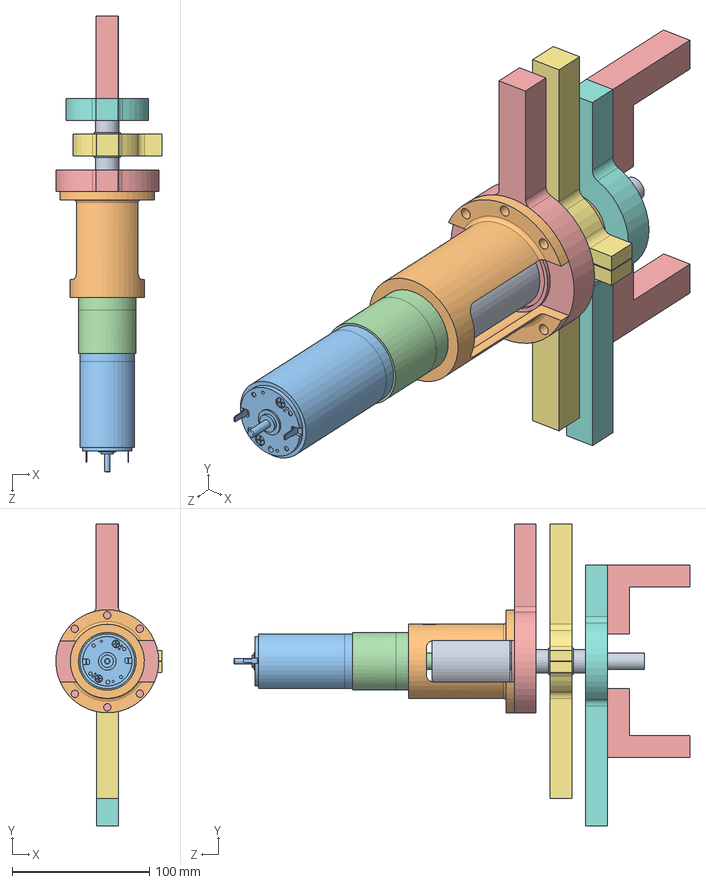
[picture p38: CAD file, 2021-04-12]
Documentation/CAD/Design_HIP16mm/Assem1.SLDASM
77.5 x 220.0 x 332.1 mm
Left_Axis
Bearing_ID15 x 2
Ring_Shaft_15mm x 2
Ring_Shaft_17mm x 2
Hip_Body
Ring_Bore_32mm x 2
Left_Hip_MLeg
Left_Hip_ILeg
Coupling_12x12mm
Motor_Shaft_Casing
RE40
Gear_N6
ILeg_Profile_Fixture x 2

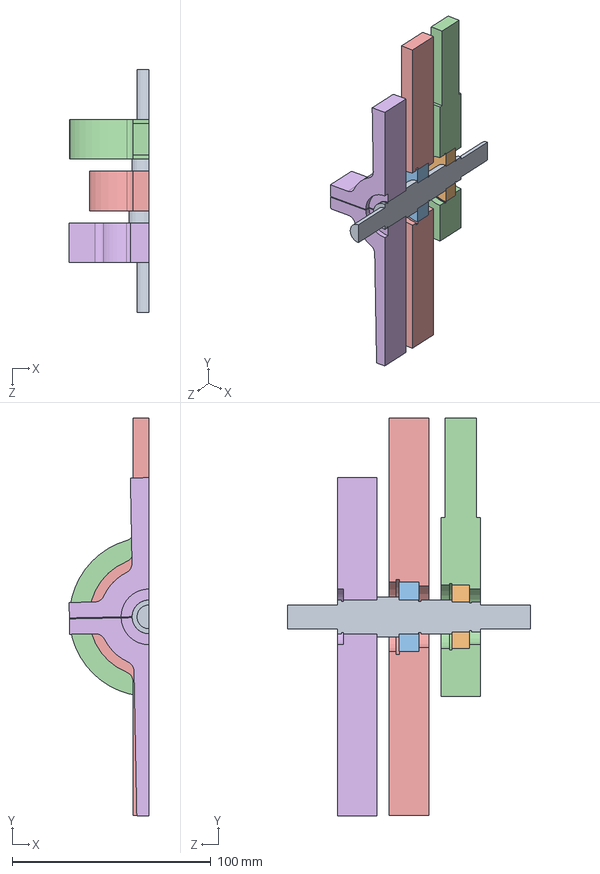
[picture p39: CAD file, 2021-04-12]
Documentation/CAD/Design_HIP20mm/Right_Hip.SLDASM
40.1 x 200.1 x 122.0 mm
Right_Axis
Bearing_ID15
Bearing_ID17
Right_Hip_Body
Right_Hip_MLeg
Right_Hip_ILeg

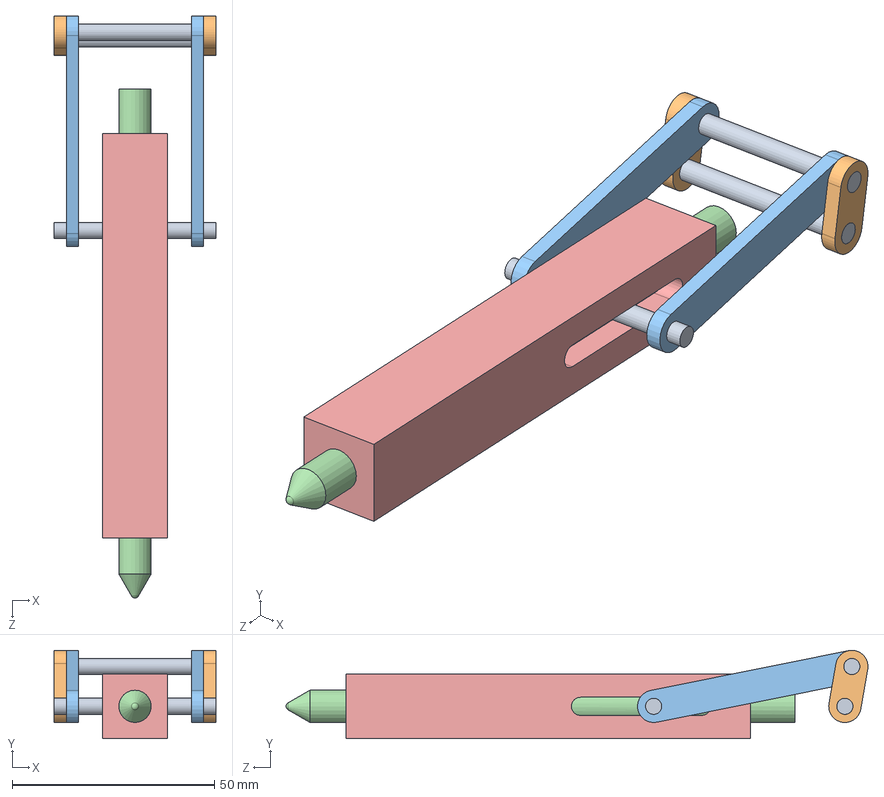
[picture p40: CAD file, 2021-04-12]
Documentation/CAD/Leg_Tip_000/Leg_Tip_Test.SLDASM
40.0 x 21.9 x 143.9 mm
Axle_D4mm_L40mm x 3
Arm x 2
Pusher_Arm x 2
Leg_Tip
Solid_Fixed_Path

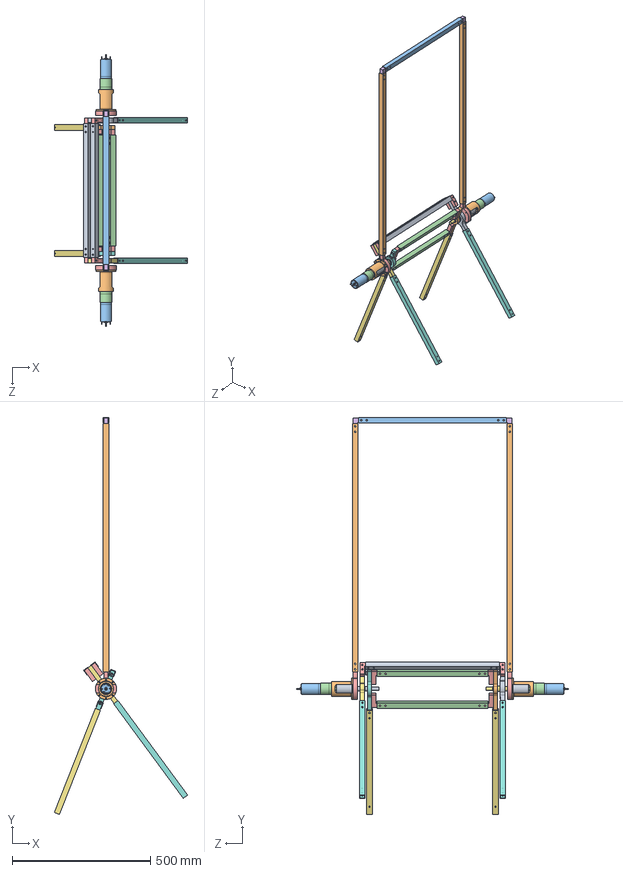
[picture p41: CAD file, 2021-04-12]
Documentation/CAD/Design_HIP16mm/Main_Assembly.SLDASM
482.8 x 1436.9 x 984.3 mm
Left_Axis
Bearing_ID15 x 3
Ring_Shaft_15mm x 3
Ring_Shaft_17mm x 4
Hip_Body x 2
Ring_Bore_32mm x 3
Left_Hip_MLeg
Left_Hip_ILeg
Coupling_12x12mm x 2
Motor_Shaft_Casing x 2
RE40 x 2
Gear_N6 x 2
ILeg_Profile_Fixture x 4
Feather_Key_4_4_15_mm x 2
Right_Axis
Bearing_ID17
Right_Hip_MLeg
Right_Hip_ILeg
Ring_Bore_35mm
ILeg_Bar x 2
MLeg_Profile_Fixture x 4
Body_Profile_Fixture x 2
ILeg_Leg x 2
MLeg_Leg x 2
MLeg_Bar x 2
Body_VerticalBar x 2
Body_Bar

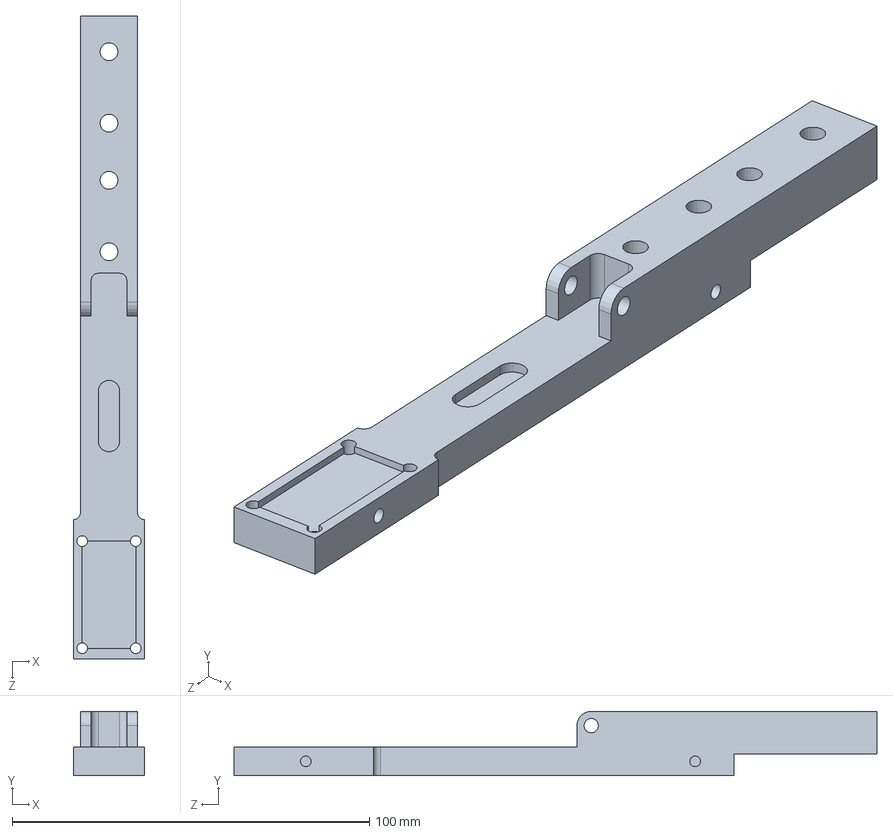
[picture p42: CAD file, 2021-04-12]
Documentation/CAD/Leg_Tip_000/Foot_Main_Body.SLDPRT
20.0 x 18.0 x 180.0 mm

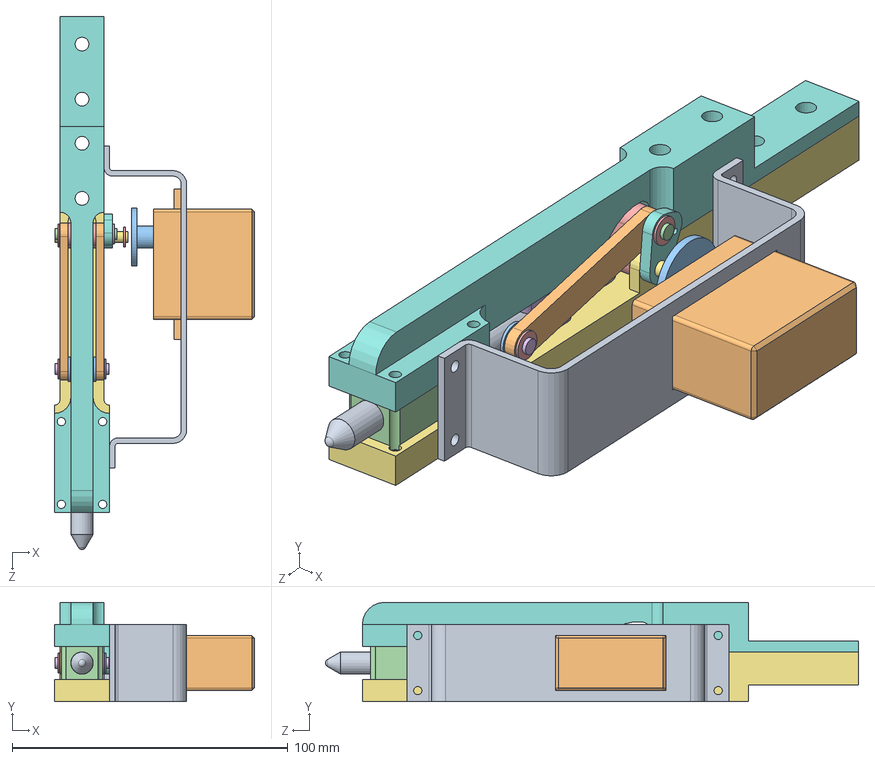
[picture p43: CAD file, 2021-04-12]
Documentation/CAD/Leg_Tip_000/Leg_Tip_Slim.SLDASM
72.6 x 36.0 x 193.4 mm
Leg_Tip
Pusher_Arm x 2
Washer_M4 x 2
PEEK_Path_Lower
Arm_10mm
PEEK_Path_Upper x 2
Foot_Main_Body
Foot_Body_Cap
Servo_Holder_Bracket
Futaba_Servo
Futaba_Servo_Flange
Axle_Cam
ExtCirclip_ShaftD4mm x 6
Axle_LegTip
Axle_Servo
SpringArm

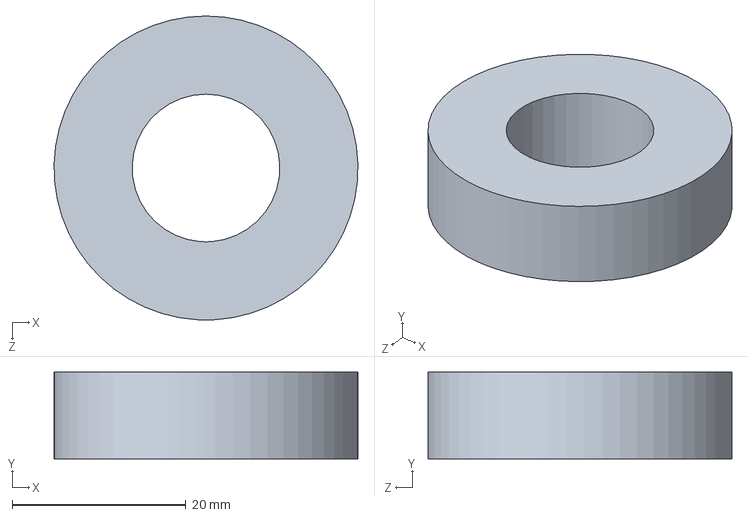
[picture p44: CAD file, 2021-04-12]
Documentation/CAD/Common_Parts/Bearing_ID17.SLDPRT
35.0 x 10.0 x 35.0 mm

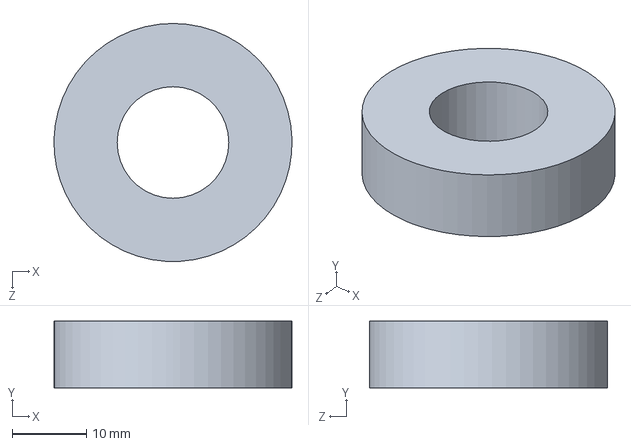
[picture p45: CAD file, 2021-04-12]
Documentation/CAD/Design_HIP16mm/Bearing_ID15.SLDPRT
32.0 x 9.00 x 32.0 mm

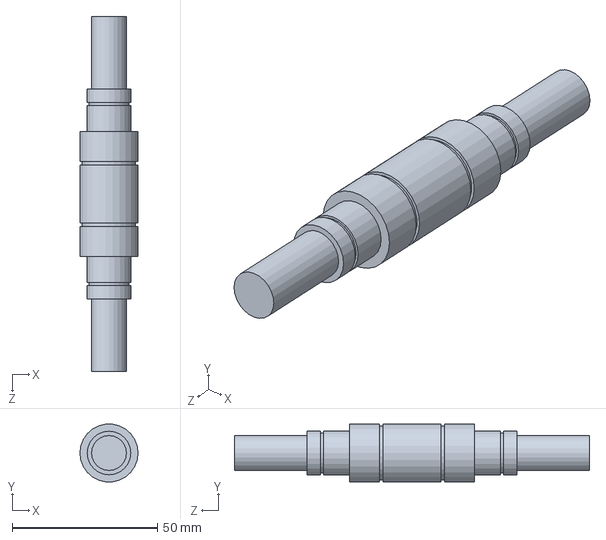
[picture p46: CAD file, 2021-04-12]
Documentation/CAD/Design_HIP20mm/Left_Axis.SLDPRT
20.0 x 19.9 x 122.0 mm

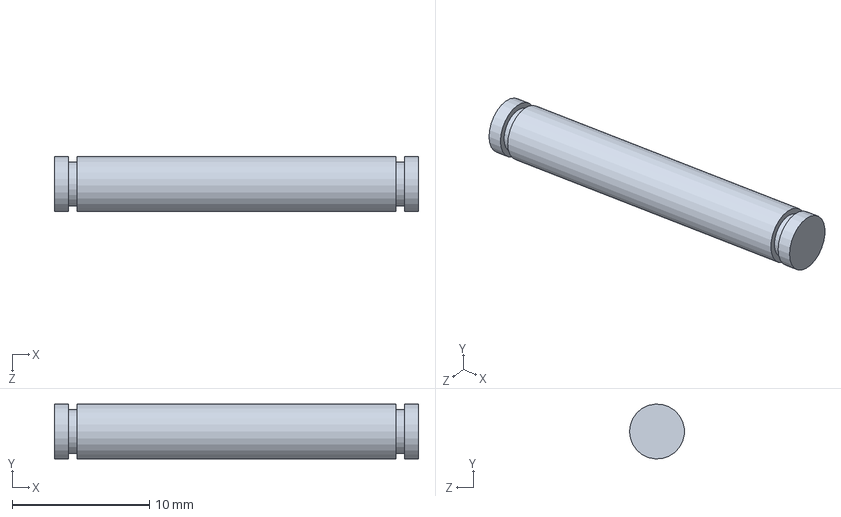
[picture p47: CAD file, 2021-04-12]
Documentation/CAD/Leg_Tip_000/Axle_Servo.SLDPRT
26.5 x 3.99 x 4.00 mm

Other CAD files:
Documentation/CAD/12_082_stp/RE40_N6_modofied_FeatherKey.SLDASM
Documentation/CAD/Leg_Tip_000/Futaba_Servo_ASM.SLDASM
Documentation/CAD/Design_HIP16mm/Left_Hip.SLDASM
Documentation/CAD/ServoCasing_E2110.stl
Documentation/CAD/12_082_stp/GP42C_1-STUFIG-203114.SLDPRT
Documentation/CAD/12_082_stp/GP42C_1-STUFIG-203114.stp
Documentation/CAD/12_082_stp/GP42C_2-STUFIG-203116.stp
Documentation/CAD/12_082_stp/GP42C_3-STUFIG-203120.stp
Documentation/CAD/12_082_stp/GP42C_4-STUFIG-203131.stp
Documentation/CAD/12_082_stp/Gear_N6.SLDPRT
Documentation/CAD/12_082_stp/RE40-148866.SLDPRT
Documentation/CAD/12_082_stp/RE40-148866.stp
Documentation/CAD/12_082_stp/RE40.SLDPRT
Documentation/CAD/Common_Parts/Bearing_ID20.SLDPRT
Documentation/CAD/Design_HIP16mm/Bearing_ID17.SLDPRT
Documentation/CAD/Design_HIP16mm/Bearing_ID20.SLDPRT
Documentation/CAD/Design_HIP16mm/Body_Bar.SLDDRW
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

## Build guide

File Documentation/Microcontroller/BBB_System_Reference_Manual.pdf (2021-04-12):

REF: BBONEBLK_SRM | BeagleBone Black System Reference Manual
Rev A5.2

## BeagleBone Black

## System

## Reference Manual

Revision A5.2
April 11, 2013

Author: Gerald Coley

Contributing Editor: Robert P J Day

THIS DOCUMENT

This work is licensed under the Creative Commons Attribution-Share Alike 3.0 Unported License. To view a copy of this license, visit http://creativecommons.org/licenses/by-sa/3.0/ (http://creativecommons.org/licenses/by-sa/3.0/) or send a letter to Creative Commons, 171 Second Street, Suite 300, San Francisco, California, 94105, USA.

All derivative works are to be attributed to Gerald Coley of BeagleBoard.org.

For more information, see http://creativecommons.org/license/results-one?license_code=by-sa (http://creativecommons.org/license/results-one?license_code=by-sa)

Send all comments and errors concerning this document to the author at gerald@beagleboard.org

For other questions you may contact Gerald at:

Gerald Coley
Texas Instruments
12500 TI Blvd. Dallas, Tx 75243 g-coley1@ti.com

All information in this document is subject to change without notice.

For an up to date version of this document refer to:

http://circuitco.com/support/index.php?title=BeagleBoneBlack#LATEST_PRODUCTION_FILES_.28A5A.29 (http://circuitco.com/support/index.php?title=BeagleBoneBlack#LATEST_PRODUCTION_FILES_.28A5A.29)

BEAGLEBONE DESIGN

These design materials referred to in this document are *NOT SUPPORTED* and DO NOT constitute a reference design. Only “community” support is allowed via resources at BeagleBoard.org/discuss.

THERE IS NO WARRANTY FOR THE DESIGN MATERIALS, TO THE EXTENT PERMITTED BY APPLICABLE LAW. EXCEPT WHEN OTHERWISE STATED IN WRITING THE COPYRIGHT HOLDERS AND/OR OTHER PARTIES PROVIDE THE DESIGN MATERIALS “AS IS” WITHOUT WARRANTY OF ANY KIND, EITHER EXPRESSED OR IMPLIED, INCLUDING, BUT NOT LIMITED TO, THE IMPLIED WARRANTIES OF MERCHANTABILITY AND FITNESS FOR A PARTICULAR PURPOSE. THE ENTIRE RISK AS TO THE QUALITY AND PERFORMANCE OF THE DESIGN MATERIALS IS WITH YOU. SHOULD THE DESIGN MATERIALS PROVE DEFECTIVE, YOU ASSUME THE COST OF ALL NECESSARY SERVICING, REPAIR OR CORRECTION.

This board was designed as an evaluation and development tool. It was not designed with any other application in mind. As such, these design materials may or may not be suitable for any other purposes. If used, the design material becomes your responsibility as to whether or not it meets your specific needs or your specific applications and may require changes to meet your requirements.

### BEAGLEBONE BLACK ADDITIONAL TERMS

BeagleBoard.org, Circuitco, LLC, and BeagleBoard.org (Supplier) provide the enclosed BeagleBone under the following conditions:

The user assumes all responsibility and liability for proper and safe handling of the goods. Further, the user indemnifies Supplier from all claims arising from the handling
or use of the goods.

Should the BeagleBone not meet the specifications indicated in the System Reference Manual, the BeagleBone may be returned within 90 days from the date of delivery to the distributor of purchase for a full refund. THE FOREGOING LIMITED WARRANTY IS THE EXCLUSIVE WARRANTY MADE BY SELLER TO BUYER AND IS IN LIEU OF ALL OTHER WARRANTIES, EXPRESSED, IMPLIED, OR STATUTORY, INCLUDING ANY WARRANTY OF MERCHANTABILITY OR FITNESS FOR ANY PARTICULAR PURPOSE. EXCEPT TO THE EXTENT OF THE INDEMNITY SET FORTH ABOVE, NEITHER PARTY SHALL BE LIABLE TO THE OTHER FOR ANY INDIRECT, SPECIAL, INCIDENTAL, OR CONSEQUENTIAL DAMAGES.

Please read the System Reference Manual and, specifically, the Warnings and Restrictions notice in the Systems Reference Manual prior to handling the product. This notice contains important safety information about temperatures and voltages.

No license is granted under any patent right or other intellectual property right of Supplier covering or relating to any machine, process, or combination in which such Supplier products or services might be or are used. The Supplier currently deals with a variety of customers for products, and therefore our arrangement with the user is not exclusive. The Supplier assume no liability for applications assistance, customer product design, software performance, or infringement of patents or services described herein.

UNITED STATES FCC AND CANADA IC REGULATORY COMPLIANCE INFORMATION

The BeagleBone is annotated to comply with Part 15 of the FCC Rules. Operation is subject to the following two conditions: (1) This device may not cause harmful interference, and (2) this device must accept any interference received, including interference that may cause undesired operation. Changes or modifications not expressly approved by the party responsible for compliance could void the user’s authority to operate the equipment.

This Class A or B digital apparatus complies with Canadian ICES-003. Changes or modifications not expressly approved by the party responsible for compliance could void the user’s authority to operate the equipment. Cet appareil numérique de la classe A ou B est conforme à la norme NMB-003 du Canada. Les changements ou les modifications pas expressément approuvés par la partie responsible de la conformité ont pu vider l’autorité de l'utilisateur pour actionner l'équipement.

BEAGLEBONE WARNINGS,

### RESTRICTIONS AND DISCLAIMERS

For Feasibility Evaluation Only, in Laboratory/Development Environments. The BeagleBone Black is not a complete product. It is intended solely for use for preliminary feasibility evaluation in laboratory/development environments by technically qualified electronics experts who are familiar with the dangers and application risks associated with handling electrical mechanical components, systems and subsystems. It should not be used as all or part of a finished end product.

Your Sole Responsibility and Risk you acknowledge, represent, and agree that:

1. You have unique knowledge concerning Federal, State and local regulatory requirements (including but not limited to Food and Drug Administration regulations, if applicable) which relate to your products and which relate to your use (and/or that of your employees, affiliates, contractors or designees) of the BeagleBone for evaluation, testing and other purposes.
2. You have full and exclusive responsibility to assure the safety and compliance of your products with all such laws and other applicable regulatory requirements, and also to assure the safety of any activities to be conducted by you and/or your employees, affiliates, contractors or designees, using the BeagleBone. Further, you are responsible to assure that any interfaces (electronic and/or mechanical) between the BeagleBone and any human body are designed with suitable isolation and means to safely limit accessible leakage currents to minimize the risk of electrical shock hazard.
3. Since the BeagleBone is not a completed product, it may not meet all applicable regulatory and safety compliance standards which may normally be associated with similar items. You assume full responsibility to determine and/or assure compliance with any such standards and related certifications as may be applicable. You will employ reasonable safeguards to ensure that your use of the BeagleBone will not result in any property damage, injury or death, even if the BeagleBone should fail to perform as described or expected.

Certain Instructions. It is important to operate the BeagleBone Black within Supplier’s recommended specifications and environmental considerations per the user guidelines. Exceeding the specified BeagleBone ratings (including but not limited to input and output voltage, current, power, and environmental ranges) may cause property damage, personal injury or death. If there are questions concerning these ratings please contact the Supplier representative prior to connecting interface electronics including input power and intended loads. Any loads applied outside of the specified output range may result in unintended and/or inaccurate operation and/or possible permanent damage to the BeagleBone and/or interface electronics. Please consult the System Reference Manual prior to connecting any load to the BeagleBone output. If there is uncertainty as to the load specification, please contact the Supplier representative. During normal operation, some circuit components may have case temperatures greater than 60 C as long as the input and output are maintained at a normal ambient operating temperature. These components include but are not limited to linear regulators, switching transistors, pass transistors, and current sense resistors which can be identified using the BeagleBone schematic located at the link in the BeagleBone System Reference Manual. When placing measurement probes near these devices during normal operation, please be aware that these devices may be very warm to the touch. As with all electronic evaluation tools, only qualified personnel knowledgeable in electronic measurement and diagnostics normally found in development environments should use the BeagleBone.

Agreement to Defend, Indemnify and Hold Harmless. You agree to defend, indemnify and hold the Suppliers, its licensors and their representatives harmless from and against any and all claims, damages, losses, expenses, costs and liabilities (collectively, "Claims") arising out of or in connection with any use of the BeagleBone that is not in accordance with the terms of the agreement. This obligation shall apply whether Claims
arise under law of tort or contract or any other legal theory, and even if the BeagleBone
fails to perform as described or expected.

Safety-Critical or Life-Critical Applications. If you intend to evaluate the components for possible use in safety critical applications (such as life support) where a failure of the Supplier’s product would reasonably be expected to cause severe personal injury or death, such as devices which are classified as FDA Class III or similar classification, then you must specifically notify Suppliers of such intent and enter into a separate Assurance and Indemnity Agreement.

Mailing Address:

BeagleBoard.org
1380 Presidential Dr. #100 Richardson, TX 75081
U.S.A.

WARRANTY: The BeagleBone Black Assembly as purchased is warranted against defects in materials and workmanship for a period of 90 days from purchase. This warranty does not cover any problems occurring as a result of improper use, modifications, exposure to water, excessive voltages, abuse, or accidents. All boards will be returned via standard mail if an issue is found. If no issue is found or express return is needed, the customer will pay all shipping costs.

## Before returning the board, please visit BeagleBoard.org/support

## For up to date SW images and technical information refer to http://circuitco.com/support/index.php?title=BeagleBoneBlack

## All support for this board is provided via community support at www.beagleboard.org/discuss

To return a defective board for repair, please request an RMA at http://beagleboard.org/support/rma

## Please DO NOT return the board without approval from the

RMA team first.
All boards received without RMA approval will not be worked on.

## Table of Contents

8.1 | BEAGLEBONEBLACK CAPE COMPATIBILITY | 82
8.1.1 | LCD Pins | 82
8.1.2 | eMMC Pins | 83
8.2 | EEPROM | 84
8.2.1 | EEPROM Address | 85
8.2.2 | I2C Bus | 85
8.2.3 | EEPROM Write Protect | 85
8.2.4 | EEPROM Data Format | 87
8.2.5 | Pin Usage | 88
8.3 | PIN USAGE CONSIDERATION | 92
8.3.1 | Boot Pins | 92
8.4 | EXPANSION CONNECTORS | 93
8.4.1 | Non-Stacking Headers-Single Cape | 93
8.4.2 | Main Expansion Headers-Stacking | 94
8.4.3 | Stacked Capes w/Signal Stealing | 95
8.4.4 | Retention Force | 96
8.4.5 | BeagleBone Black Female Connectors | 96
8.5 | SIGNAL USAGE | 97
8.6 | CAPE POWER | 97
8.6.1 | Main Board Power | 97
8.6.2 | Expansion Board External Power | 98
8.7 | MECHANICAL | 98
8.7.1 | Standard Cape Size | 98
8.7.2 | Extended Cape Size | 99
8.7.3 | Enclosures | 100

### 9.0 BEAGLEBONE BLACK MECHANICAL | 101

9.1 | DIMENSIONS AND WEIGHT | 101
9.2 | SILKSCREEN AND COMPONENT LOCATIONS | 102

### 10.0 PICTURES | 105

### 11.0 SUPPORT INFORMATION | 107

11.1 | HARDWARE DESIGN | 107
11.2 | SOFTWARE UPDATES | 107
11.3 | RMA SUPPORT | 108

## Figures

Figure 1. | In The Box | 13
Figure 2. | Tethered Configuration | 14
Figure 3. | USB Connection to the Board | 15
Figure 4. | Board Power LED | 15
Figure 5. | Board Boot Status | 16
Figure 6. | Desktop Configuration | 17
Figure 7. | Connect microHDMI Cable to the Monitor | 18
Figure 8. | DVI-D to HDMI Adapter | 18
Figure 9. | Wireless Keyboard and Mouse Combo | 19
Figure 10. | Connect Keyboard and Mouse Receiver to the Board | 19
Figure 11. | Keyboard and Mouse Hubs | 19
Figure 12. | Ethernet Cable Connection | 20

Figure 59. | Expansion Connector | 94
Figure 60. | Stacked Cape Expansion Connector | 95
Figure 61. | Stacked w/Signal Stealing Expansion Connector | 96
Figure 62. | Connector Pin Insertion Depth | 96
Figure 63. | Cape Board Dimensions | 99
Figure 64. | Board Dimensions | 102
Figure 65. | Component Side Silkscreen | 103
Figure 66. | Component Side Silkscreen | 104
Figure 67. | Top Side | 105
Figure 68. | Bottom Side | 106
Figure 69. | Bottom Side | 108

## Tables

Table 1. | Change History | 12
Table 2. | BeagleBone Black Features | 26
Table 3. | BeagleBone Black Battery Pins | 40
Table 4. | BeagleBone Black Power Consumption(mA@5V) | 41
Table 5. | Processor Features | 49
Table 6. | eMMC Boot Pins | 54
Table 7. | User LED Control Signals/Pins | 56
Table 8. | HDMI Supported Monitor Resolutions | 63
Table 9. | TDA19988 I2C Address | 65
Table 10. | Expansion Header P8 Pinout | 70
Table 11. | Expansion Header P9 Pinout | 72
Table 12. | P8 LCD Conflict Pins | 82
Table 13. | P8 eMMC Conflict Pins | 83
Table 14. | Expansion Board EEPROM | 87
Table 15. | EEPROM Pin Usage | 89
Table 16. | Single Cape Connectors | 94
Table 17. | Stacked Cape Connectors | 95
Table 18. | Expansion Voltages | 97

### 1.0 Introduction

This document is the System Reference Manual for the BeagleBone Black and covers its use and design. The board will primarily be referred to in the remainder of this document simply as the board, although it may also be referred to as the BeagleBone Black as a reminder. There are also references to the original BeagleBone as well, and will be referenced as simply BeagleBone.

This design is subject to change without notice as we will work to keep improving the design as the product matures based on feedback and experience. Software updates will be frequent and will be independent of the hardware revisions and as such not result in a change in the revision number.

Make sure you check the support Wiki frequently for the most up to date information.

http://circuitco.com/support/index.php?title=BeagleBoneBlack

### 2.0 Change History

This section describes the change history of this document and board. Document changes are not always a result of a board change. But aboard change will always result in a document change.

### 2.1 Document Change History

Table 1. | Change History
Rev | Changes | Date | By
A4 | Preliminary | January 4, 2013 | GC
A5 | Production release | January 8.2013 | GC
A5.1 | 1. Added information on Power button and the battery access points. 2. Final production released version. | April 1 2013 | GC
A5.2 | 1. Edited version. 2. Added numerous pictures of the Rev A5A board. | April 23 2013 | GC

### 2.2 Board Changes

### 2.2.1 Rev A5B

This is the initial production release of the board. We will be tracking changes from this point forward.

### 3.0 Connecting Up Your BeagleBone Black

This section provides instructions on how to hook up your board. Two scenarios will be discussed:

1) Tethered to a PC and
2) As a standalone development platform in a desktop PC configuration.

### 3.1 What’s In the Box

In the box you will find three main items as shown in Figure 1.

- BeagleBone Black
- miniUSB to USB Type A Cable
- Instruction card
3
This is sufficient for the tethered scenario and creates an out of box experience where the board can be used immediately with no other equipment needed.

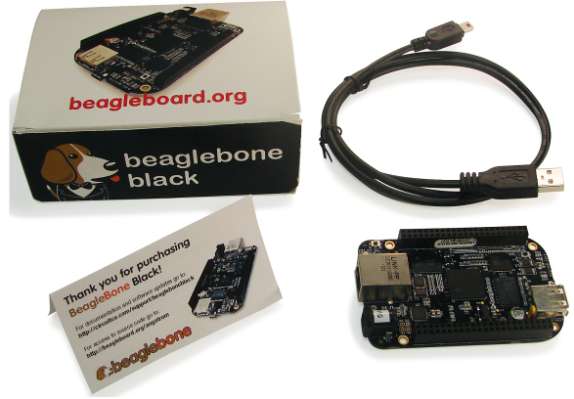
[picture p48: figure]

Figure 1. In The Box

### 3.2 Main Connection Scenarios

This section will describe how to connect the board for use. This section is basically a slightly more detailed description of the Quick Start Guide that came in the box. There is also a Quick Start Guide document on the board that should also be refereed. The intent here is that someone looking t purchase the board will be able to read this section and get a good idea as to what the initial set up will be like.

The board can be configured in several different ways, but we will discuss the two most common scenarios as described in the Quick Start Guide card that comes in the box.

- Tethered to a PC via the USB cable
- Board is accessed as a storage drive
- Or a RNDIS Ethernet connection.
- Standalone desktop
- Display
- Keyboard and mouse
- External 5V power supply

Each of these configurations is discussed in general terms in the following sections.

For an up-to-date list of confirmed working accessories please go to http://circuitco.com/support/index.php?title=BeagleBone_Black_Accessories

### 3.3 Tethered To A PC

In this configuration, the board is powered by the PC via the provided USB cable--no other cables are required. The board is accessed either as a USB storage drive or via the browser on the PC. You need to use either Firefox or Chrome on the PC, IEx will not work properly. Figure 2 shows this configuration.

Figure 2. Tethered Configuration

All the power for the board is provided by the PC via the USB cable. In some instances, the PC may not be able to supply sufficient power for the board. In that case, an external 5VDC power supply can be used, but this should rarely be necessary.

### 3.3.1 Connect the Cable to the Board

1. Connect the small connector on the USB cable to the board as shown in Figure 4. The connector is on the bottom side of the board.

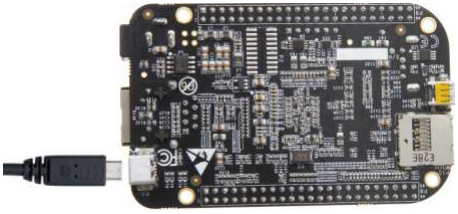
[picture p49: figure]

Figure 3. USB Connection to the Board

2. Connect the large connector of the USB cable to your PC or laptop USB port.
3. The board will power on and the power LED will be on as shown in Figure 4 below.

Figure 4. Board Power LED

4. When the board starts to boot the LEDs will come on in sequence as shown in Figure 5 below. It will take a few seconds for the status LEDs to come on, so be patient. The LEDs will be flashing in an erratic manner as it boots the Linux kernel.

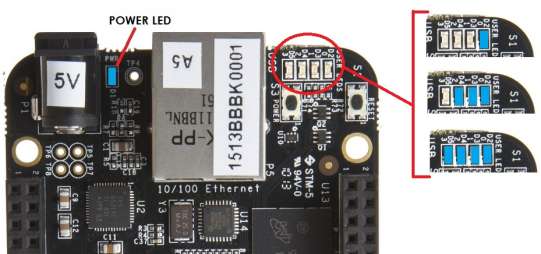
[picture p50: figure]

Figure 5. Board Boot Status

### 3.3.2 Accessing the Board as a Storage Drive

The board will appear around a USB Storage drive on your PC after the kernel has booted, which will take a round 10 seconds. The kernel on the board needs to boot before the port gets enumerated. Once the board appears as a storage drive, do the following:

1) Open the USB Drive folder.
2) Click on the file named start.html
3) The file will be opened by your browser on the PC and you should get a display showing the Quick Start Guide.
4) Your board is now operational! Follow the instructions on your PC screen.

### 3.4 Standalone w/Display and Keyboard/Mouse

In this configuration, the board works more like a PC, totally free from any connection to a PC as shown in Figure 6. It allows you to create your code to make the board do whatever you need it to do. It will however require certain common PC accessories. These accessories and instructions are described in the following section.

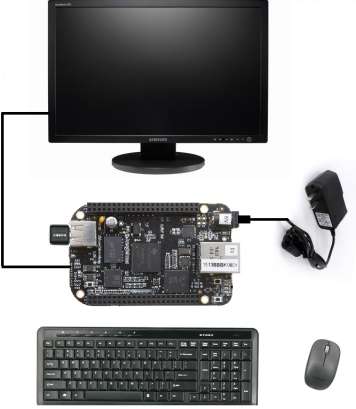
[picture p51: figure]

Figure 6. Desktop Configuration

Optionally an Ethernet cable can also be used for network access.

### 3.4.1 Required Accessories

In order to use the board in this configuration, you will need the following accessories:

- (1) 5VDC 1A power supply
- (1) HDMI monitor or a DVI-D monitor with an adapter. (NOTE: Only HDMI will give you audio capability).
- (1) Micro HDMI to HDMI cable
- (1) USB wireless keyboard and mouse combo.
- (1) USB HUB (OPTIONAL). The board has only one USB host port, so you may need to use a USB Hub if your keyboard and mouse requires two ports.

For an up-to-date list of confirmed working accessories please go to http://circuitco.com/support/index.php?title=BeagleBone_Black_Accessories

### 3.4.2 Connecting Up the Board

1. Connect the big end of the HDMI cable as shown in Figure 7 to your HDMI monitor. Refer to your monitor Owner’s Manual for the location of your HDMI port. If you have a DVI-D Monitor go to Step 3, otherwise proceed to Step 4.

Figure 7. Connect microHDMI Cable to the Monitor

### NOTE: Do not plug in the cable to the board until after the

board is powered up.

2. If you have a DVI-D monitor you must use a DVI-D to HDMI adapter in addition to your HDMI cable. An example is shown in Figure 8 below from two perspectives.

Figure 8. DVI-D to HDMI Adapter

To the Monitor

To microHDMI
Cable

3. If you have a single wireless keyboard and mouse combination such as seen in Figure 9 below, you need to plug the receiver in the USB host port of the board as shown in Figure 10.

Figure 9. Wireless Keyboard and Mouse Combo

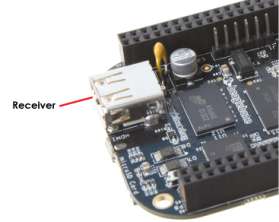
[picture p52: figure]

Figure 10. Connect Keyboard and Mouse Receiver to the Board
If you have a wired USB keyboard requiring two USB ports, you will need a HUB similar to the ones shown in Figure 11. You may want to have more than one port for other devices. Note that the board can only supply up to 500mA, so if you plan to load it down, it will need to be externally powered.

Figure 11. Keyboard and Mouse Hubs

4. Connect the Ethernet Cable

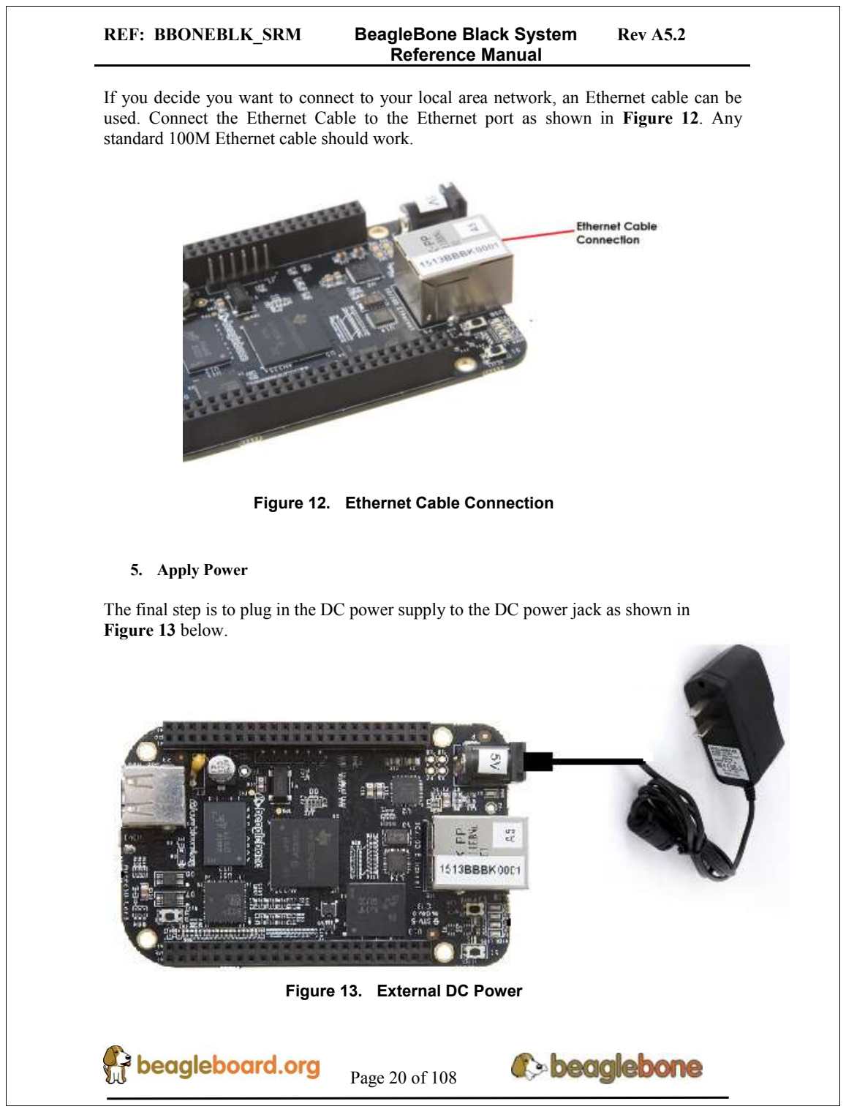
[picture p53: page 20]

If you decide you want to connect to your local area network, an Ethernet cable can be used. Connect the Ethernet Cable to the Ethernet port as shown in Figure 12. Any standard 100M Ethernet cable should work.

Figure 12. Ethernet Cable Connection

### 5. Apply Power

The final step is to plug in the DC power supply to the DC power jack as shown in Figure 13 below.

Figure 13. External DC Power

6. The cable needed to connect to your display is a microHDMI to HDMI. Connect the microHDMI connector end to the board at this time. The connector is on the bottom side of the board as shown in Figure 14 below.

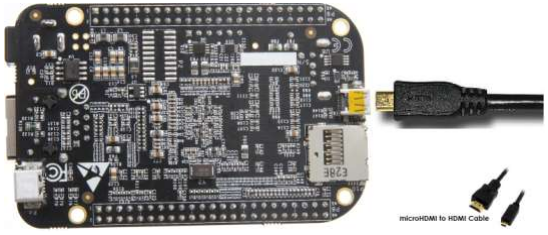
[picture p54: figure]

Figure 14. Connect microHDMI Cable to the Board

The connector is fairly robust, but we suggest that you not use the cable as a leash for your Beagle. Take proper care not to put too much stress on the connector or cable.

7. Booting the Board

As soon as the power is applied to the board, it will start the booting up process. When the board starts to boot the LEDs will come on in sequence as shown in Figure 15 below. It will take a few seconds for the status LEDs to come on, so be patient. The LEDs will be flashing in an erratic manner as it boots the Linux kernel.

Figure 15. Board Boot Status While the four user LEDS can be over written and used as desired, they do have specific meanings in the image that is shipped with the board once the Linux kernel has booted.

- USER0 is the heartbeat indicator from the Linux kernel.
- USER1 turns on when the SD card is being accessed
- USER2 is an activity indicator. It turns on when the kernel is not in the idle loop.
- USER3 turns on when the onboard eMMC is being accessed.
8. A Booted System
1. The board will have a mouse pointer appear on the screen as it enters the Linux boot step. You may have to move the physical mouse to get the mouse pointer to appear. The system can come up in the suspend mode with the HDMI port in a sleep mode.
2. After a minute or two a login screen will appear. You do not have to do anything at this point.
3. After a minute or two the desktop will appear. It should be similar to the one shown in Figure 16. HOWEVER, it will change from one release to the next, so do not expect your system to look exactly like the one in the figure, but it will be very similar.
4. And at this point you are ready to go! Figure 16 shows the desktop after booting.

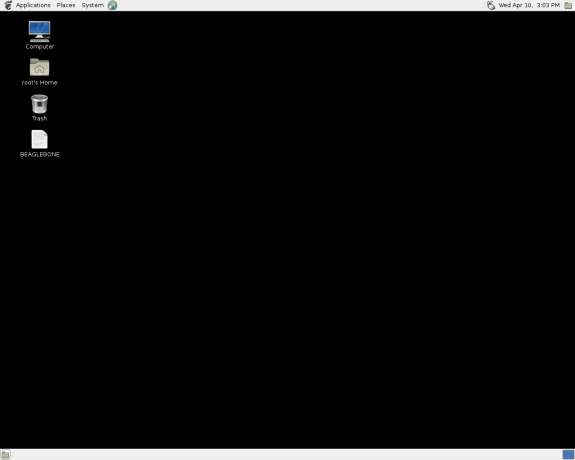
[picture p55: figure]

Figure 16. Desktop Screen

NOTE: At press time this is what the default screen looks like. If you see something different, do not be alarmed. It is intended. Once the final screen is finalized, this document will be updated and available for download.

### 4.0 BeagleBone Black Overview

The BeagleBone Black is the latest addition to the BeagleBoard.org family and like its predecessors, is designed to address the Open Source Community, early adopters, and anyone interested in a low cost ARM Cortex-A8 based processor.

It has been equipped with a minimum set of features to allow the user to experience the power of the processor and is not intended as a full development platform as many of the features and interfaces supplied by the processor are not accessible from the BeagleBone Black via onboard support of some interfaces. It is not a complete product designed to do any particular function. It is a foundation for experimentation and learning how to program the processor and to access the peripherals by the creation of your own software and hardware.

It also offers access to many of the interfaces and allows for the use of add-on boards called capes, to add many different combinations of features. A user may also develop their own board or add their own circuitry.

BeagleBone Black is manufactured and warranted by Circuitco LLC in Richardson Texas for the benefit of the community and its supporters. In addition, Circuitco provides the RMA support for the BeagleBone Black.

Jason Kridner of Texas Instruments handles the community promotions and is the spokesmen for BeagleBoard.org.

The board is designed by Gerald Coley, an employee of Texas Instruments and a charter member of the BeagleBoard.org community.

The PCB layout was done by Circuitco and Circuitco is the sole funder of its development and transition to production.

The Software is written and supported by the thousands of community members, including Jason Kridner, employees of Texas Instruments, DigiKey, and Circuitco.

### 4.1 BeagleBone Compatibility

The board is intended to be compatible with the original BeagleBone as much as possible. There are several areas where there are differences between the two designs. These differences are listed below, along with the reasons for the differences.

- Sitara XAM3359AZCZ100, 1GHZ, processor.
- Sorry, we just had to make it faster.
- 512MB DDR3L
- Cost reduction
- Performance boost
- Memory size increase
- Lower power
- No Serial port by default.
- Cost reduction
- Can be added by buying a TTL to USB Cable that is widely available
- Single most cost reduction action taken
- No JTAG emulation over USB.
- Cost reduction
- JTAG header is not populated, but can easily be mounted.
- Onboard Managed NAND (eMMC)
- 2GB
- Cost reduction
- Performance boost x8 vs. x4 bits
- Performance boost due to deterministic properties vs. SD card
- GPMC bus may not be accessible from the expansion headers in some cases
- Result of eMMC on the main board
- Signals are still routed to the expansion connector
- If eMMC is not used, signals can be used via expansion if eMMC is held in reset
- There may be 10 less GPIO pins available
- Result of eMMC
- If eMMC is not used, could still be used
- The power expansion header, for battery and backlight, has been removed
- Cost reduction
- Space reduction
- Four pins were added to provide access to the battery charger function.
- HDMI interface onboard
- Feature addition
- Audio and video capable
- Micro HDMI
- No three function USB cable
- Cost reduction

### 4.2 BeagleBone Black Features and Specification

This section covers the specifications and features of the board and provides a high level description of the major components and interfaces that make up the board.

Table 2 provides a list of the features.

Table 2. | BeagleBone Black Features
| Feature
Processor | Sitara AM3359AZCZ100 1GHz, 2000 MIPS
Graphics Engine | SGX530 3D, 20M Polygons/S
SDRAM Memory | 512MB DDR3L 606MHZ
Onboard Flash | 2GB, 8bit Embedded MMC
PMIC | TPS65217C PMIC regulator and one additional LDO.
Debug Support | Optional Onboard 20-pin CTI JTAG, Serial Header
Power Source | miniUSB USB or DC Jack | 5VDC External Via Expansion Header
PCB | 3.4” x 2.1” | 6 layers
Indicators | 1-Power, 2-Ethernet, 4-User Controllable LEDs
HS USB 2.0 Client Port | Access to USB0, Client mode via miniUSB
HS USB 2.0 Host Port | Access to USB1, Type A Socket, 500mA LS/FS/HS
Serial Port | UART0 access via 6 pin 3.3V TTL Header. Header is populated
Ethernet | 10/100, RJ45
SD/MMC Connector | microSD , 3.3V
User Input | Reset Button Boot Button Power Button
Video Out | 16b HDMI, 1280x1024 (MAX) 1024x768,1280x720,1440x900 w/EDID Support
Audio | Via HDMI Interface, Stereo
Expansion Connectors | Power 5V, 3.3V , VDD_ADC(1.8V) 3.3V I/O on all signals McASP0, SPI1, I2C, GPIO(65), LCD, GPMC, MMC1, MMC2, 7 AIN(1.8V MAX), 4 Timers, 3 Serial Ports, CAN0, EHRPWM(0,2),XDMA Interrupt, Power button, Expansion Board ID (Up to 4 can be stacked)
Weight | 1.4 oz (39.68 grams)
Power | Refer to Section 6.1.7

### 4.3 Board Component Locations

This section describes the key components on the board. It provides information on their location and function. Familiarize yourself with the various components on the board.

### 4.3.1 Connectors, LEDs, and Switches

Figure 17 below shows the locations of the connectors, LEDs, and switches on the PCB layout of the board.

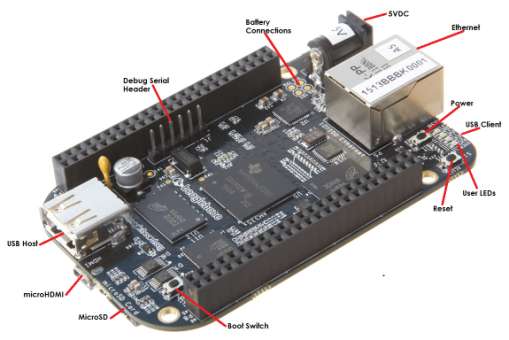
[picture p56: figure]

Figure 17. Connectors, LEDs and Switches

- DC Power is the main DC input that accepts 5V power.
- Power Button alerts the processor to initiate the power down sequence.
- 10/100 Ethernet is the connection to the LAN.
- Serial Debug is the serial debug port.
- USB Client is a miniUSB connection to a PC that can also power the board.
- BOOT switch can be used to force a boot from the SD card.
- There are four blue LEDS that can be used by the user.
- Reset Button allows the user to reset the processor.
- uSD slot is where a uSD card can be installed.
- microHDMI connector is where the display is connected to.
- USB Host can be connected different USB interfaces such as Wi-Fi, BT, Keyboard, etc.

### 4.3.2 Key Components

Figure 18 below shows the locations of the key components on the PCB layout of the board.

Figure 18. Key Components

- Sitara AM3359AZCZ100 is the processor for the board.
- Micron 512MB DDR3L is the Dual Data Rate RAM memory.
- TPS65217C PMIC provides the power rails to the various components on the board.
- SMSC Ethernet PHY is the physical interface to the network.
- Micron eMMC is an onboard MMC chip that holds up to 2GB of data.
- HDMI Framer provides control for an HDMI or DVI-D display with an adapter.

### 5.0 BeagleBone Black High Level Specification

This section provides the high level specification of the BeagleBone Black.

### 5.1 Block Diagram

Figure 19 below is the high level block diagram of the BeagleBone Black.

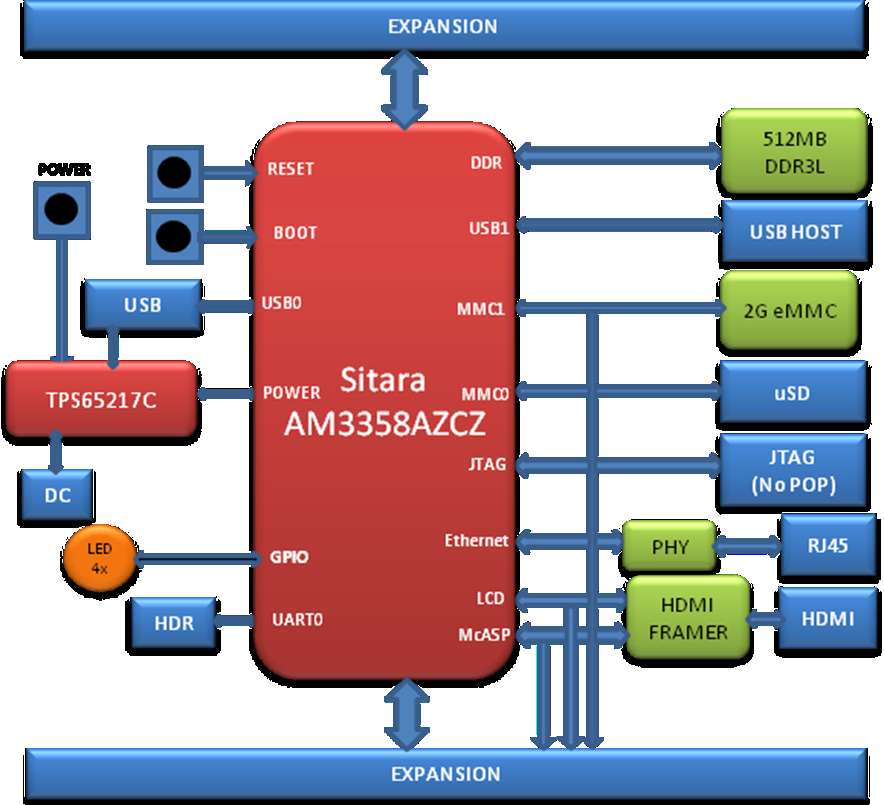
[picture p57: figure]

Figure 19. BeagleBone Black Key Components

### 5.2 Processor

For the initial release, the board uses the Sitara XAM3359AZCZ processor in the 15x15 package. This is basically the same processor as used on the original BeagleBone. It does use the updated 2.0 revision with several fixes on this new processor as opposed to the original BeagleBone. A couple of important features from this new processor include:

- 1GHZ Operation
- RTC fix

Eventually the board will move to the Sitara AM3358BZCZ100 device once released and readily available from TI. At this time we do not have a date when this will happen. We do not expect any benefit from moving to this device and there should be no impact seen as a result of making this move,

### 5.3 Memory

Described in the following sections are the three memory devices found on the board.

5.3.1 512MB DDR3L

A single 256Mb x16 DDR3L 4Gb (512MB) memory device is used. The memory used is the MT41K512M16HA-125 from Micron. It will operate at a clock frequency of 303MHz yielding an effective rate of 606MHZ on the DDR3L bus allowing for 1.32GB/S of DDR3L memory bandwidth.

5.3.2 32KB EEPROM

A single 32KB EEPROM is provided on I2C0 that holds the board information. This information includes board name, serial number, and revision information. This will be the same as found on the original BeagleBone. It has a test point to allow the device to be programmed and otherwise to provide write protection when not grounded.

5.3.3 2GB Embedded MMC

A single 2GB embedded MMC (eMMC) device is on the board. The device connects to the MMC1 port of the processor, allowing for 8bit wide access. Default boot mode for the board will be MMC1 with an option to change it to MMC0 for SD card booting. MMC0 cannot be used in 8Bit mode because the lower data pins are located on the pins used by the Ethernet port. This does not interfere with SD card operation but it does make it unsuitable for use as an eMMC port if the 8 bit feature is needed.

### 5.3.4 MicroSD Connector

The board is equipped with a single microSD connector to act as the secondary boot source for the board and, if selected as such, can be the primary boot source. The connector will support larger capacity SD cards. The SD card is not provided with the board. Booting from MMC0 will be used to flash the eMMC in the production environment or can be used by the user to update the SW as needed.

### 5.3.5 Boot Modes

As mentioned earlier, there are four boot modes:

- eMMC Boot…This is the default boot mode and will allow for the fastest boot time and will enable the board to boot out of the box using the pre-flashed OS image without having to purchase an SD card or an SD card writer.
- SD Boot…This mode will boot from the uSD slot. This mode can be used to override what is on the eMMC device and can be used to program the eMMC when used in the manufacturing process or for field updates.
- Serial Boot…This mode will use the serial port to allow downloading of the software direct. A separate USB to serial cable is required to use this port.
- USB Boot…This mode supports booting over the USB port.

Software to support USB and serial boot modes is not provided by beagleboard.org. Please contact TI for support of this feature.

A switch is provided to allow switching between the modes.

- Holding the boot switch down during boot without a SD card inserted will force the boot source to be the USB port and if nothing is detected on the USB client port, it will go to the serial port for download.
- Without holding the switch, the board will boot from eMMC. If it is empty, then it will try booting from the uSD slot, followed by the serial port, and then the USB port.
- If you hold the boot switch down during boot, and you have a uSD card inserted with a bootable image, the board will boot form the uSD card.

### 5.4 Power Management

The TPS65217C power management device is used along with a separate LDO to provide power to the system. The TPS65217C version provides for the proper voltages required for the DDR3L. This is the same device as used on the original BeagleBone with the exception of the power rail configuration settings which will be changed in the internal EEPROM to the TPS65217 to support the new voltages.

DDR3L requires 1.5V instead of 1.8V on the DDR2 as is the case on the original BeagleBone. The 1.8V regulator setting has been changed to 1.5V for the DDR3L. The LDO3 3.3V rail has been changed to 1.8V to support those rails on the processor. LDO4 is still 3.3V for the 3.3V rails on the processor. An external LDOTLV70233 provides the 3.3V rail for the rest of the board.

### 5.5 PC USB Interface

The board has a miniUSB connector that connects the USB0 port to the processor. This is the same connector as used on the original BeagleBone.

### 5.6 Serial Debug Port

Serial debug is provided via UART0 on the processor via a single 1x6 pin header. In order to use the interface a USB to TTL adapter will be required. The header is compatible with the one provided by FTDI and can be purchased for about $12 to $20 from various sources. Signals supported are TX and RX. None of the handshake signals are supported.

### 5.7 USB1 Host Port

On the board is a single USB Type A female connector with full LS/FS/HS Host support that connects to USB1 on the processor. The port can provide power on/off control and up to 500mA of current at 5V. Under USB power, the board will not be able to supply the full 500mA, but should be sufficient to supply enough current for a lower power USB device supplying power between 50 to 100mA.

You can use a wireless keyboard/mouse configuration or you can add a HUB for standard keyboard and mouse interfacing.

### 5.8 Power Sources

The board can be powered from four different sources:

- A USB port on a PC
- A 5VDC 1A power supply plugged into the DC connector.
- A power supply with a USB connector.
- Expansion connectors

The USB cable is shipped with each board. This port is limited to 500mA by the Power Management IC. It is possible to change the settings in the TPS65217C to increase this current, but only after the initial boot. And, at that point the PC most likely will complain, but you can also use a dual connector USB cable to the PC to get to 1A.

The power supply is not provided with the board but can be easily obtained from numerous sources. A 1A supply is sufficient to power the board, but if there is a cape plugged into the board or you have a power hungry device or hub plugged into the host port, then more current may needed from the DC supply.

Power routed to the board via the expansion header could be provided from power derived on a cape. The DC supply should be well regulated and 5V +/-.25V.

### 5.9 Reset Button

When pressed and released, causes a reset of the board. The reset button used on the BeagleBone Black is a little larger than the one used on the original BeagleBone. It has also been moved out to the edge of the board so that it is more accessible.

### 5.10 Power Button

A power button is provided near the reset button close to the Ethernet connector. This button takes advantage of the input to the PMIC for power down features. While a lot of capes have a button, it was decided to add this feature to the board to insure everyone had access to some new features. These features include:

- Interrupt is sent to the processor to facilitate an orderly shutdown to save files and to un-mount drives.
- Provides ability to let processor put board into a sleep mode to save power.
- Can alert processor to wake up from sleep mode and restore state before sleep was entered.
- Allows board to enter the sleep mode, preserving the RTC clock

If you hold the button down longer than 8 seconds, the board will power off if you release the button when the power LED turns off. If you continue to hold it, the board will power back up completing a power cycle.

### 5.11 Indicators

There are a total of five blue LEDs on the board.

- One blue power LED indicates that power is applied and the power management IC is up. If this LED flashes when applying power, it means that an excess current flow was detected and the PMIC has shut down.
- Four blue LEDs that can be controlled via the SW by setting GPIO pins.

In addition, there are two LEDs on the RJ45 to provide Ethernet status indication. One is yellow (100M Link up if on) and the other is green (Indicating traffic when flashing).

### 5.12 CTI JTAG Header

A place for an optional 20 pin CTI JTAG header is provided on the board to facilitate the SW development and debugging of the board by using various JTAG emulators. This header is not supplied standard on the board. To use this, a connector will need to be soldered onto the board.

### 5.13 HDMI Interface

A single HDMI interface is connected to the 16 bit LCD interface on the processor. The 16b interface was used to preserve as many expansion pins as possible to allow for use by the user. The NXP TDA19988BHN is used to convert the LCD interface to HDMI and convert the audio as well. The signals are still connected to the expansion headers to enable the use of LCD expansion boards or access to other functions on the board as needed.

The HDMI device does not support HDCP copy protection. Support is provided via EDID to allow the SW to identify the compatible resolutions. Currently the following resolutions are supported via the software:

- 1280 x 1024
- 1440 x 900
- 1024 x 768
- 1280 x 720

### 5.14 Cape Board Support

The BeagleBone Black has the ability to accept up to four expansion boards or capes that can be stacked onto the expansion headers. The word cape comes from the shape of the board as it is fitted around the Ethernet connector on the main board. This notch acts as a key to insure proper orientation of the cape.

The majority of capes designed for the original BeagleBone will work on the BeagleBone Black. The two main expansion headers will be populated on the board. There are a few exceptions where certain capabilities may not be present or are limited to the BeagleBone Black. These include:

- GPMC bus may NOT be available due to the use of those signals by the eMMC. If the eMMC is used for booting only and the file system is on the SD card, then these signals could be used.
- Another option is to use the SD or serial boot modes and not use the eMMC.
- The power expansion header is not on the BeagleBone Black so those functions are not supported.

For more information on cape support refer to Section 9.0.

### 6.0 Detailed Hardware Design

This section provides a detailed description of the Hardware design. This can be useful for interfacing, writing drivers, or using it to help modify specifics of your own design.

Figure 20 below is the high level block diagram of the board.

Figure 20. BeagleBone Black Block Diagram

### 6.1 Power Section

Figure 21 is the high level block diagram of the power section of the board.

Figure 21. High Level Power Block Diagram

This section describes the power section of the design and all the functions performed by the TPS65217C.

### 6.1.1 TPS65217C PMIC

The main Power Management IC (PMIC) in the system is the TPS65217C which is a single chip power management IC consisting of a linear dual-input power path, three step-down converters, and four LDOs. The system is supplied by a USB port or DC adapter. Three high-efficiency 2.25MHz step-down converters are targeted at providing the core voltage, MPU, and memory voltage for the board.

The step-down converters enter a low power mode at light load for maximum efficiency across the widest possible range of load currents. For low-noise applications the devices can be forced into fixed frequency PWM using the I2C interface. The step-down converters allow the use of small inductors and capacitors to achieve a small footprint solution size.

LDO1 and LDO2 are intended to support system standby mode. In normal operation, they can support up to 100mA each. LDO3 and LDO4 can support up to 285mA each.

By default only LDO1 is always ON but any rail can be configured to remain up in SLEEP state. In particular the DCDC converters can remain up in a low-power PFM mode to support processor suspend mode. The TPS65217C offers flexible power-up and

PWR_BUT

PWR_EN

Interrupt

RTC_PORZ

SYS_RESET

Power Rails

I2C0

TPS65217C

DC IN

LDO
3V3 power-down sequencing and several house-keeping functions such as power-good output, pushbutton monitor, hardware reset function and temperature sensor to protect the battery.

For more information on the TPS65217C, refer to http://www.ti.com/product/tps65217C.

Figure 22 is the high level block diagram of the TPS65217C.

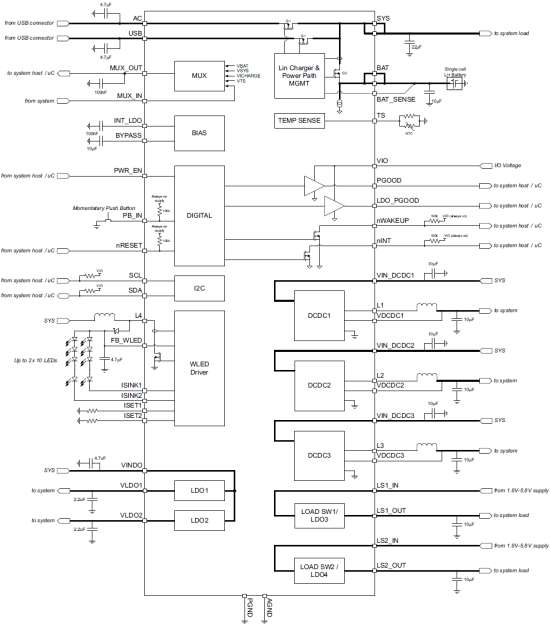
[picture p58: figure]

Figure 22. TPS65217C Block Diagram

### 6.1.2 DC Input

Figure 23 below shows how the DC input is connected to the TPS65217C.

VDD_5V

P1

PJ-200A

1

1

3

3

2

2

DGND

DGND

C1
10uF,10V

C2
10uF,10V

DGND

U2

TPS65217C

AC

10

USB

12

SYS1

7

SYS2

8

VIN_DCDC1

21

VIN_DCDC3

32

VINLDO

2

LDO3_IN

39

VIN_DCDC2

22

LDO4_IN

42

USB_DC

U4

TL5209

IN

2 | OUT

3

GND1

5 EN

1
ADJ

4

GND3

6

GND2

7 | GND4

8

DGND

VDD_3V3A

DGND

C17

2.2uF,6.3V

Figure 23. TPS65217 DC Connection

A 5VDC supply can be used to provide power to the board. The power supply current depends on how many and what type of add-on boards are connected to the board. For typical use, a 5VDC supply rated at 1A should be sufficient. If heavier use of the expansion headers or USB host port is expected, then a higher current supply will be required.

The connector used is a 2.1MM center positive x 5.5mm outer barrel. The 5VDC rail is connected to the expansion header. It is possible to power the board via the expansion headers from an add-on card. The 5VDC is also available for use by the add-on cards when the power is supplied by the 5VDC jack on the board.

### 6.1.3 USB Power

The board can also be powered from the USB port. A typical USB port is limited to 500mA max. When powering from the USB port, the VDD_5V rail is not provided to the expansion header. So capes that require the 5V rail to supply the cape direct, bypassing the TPS65217C, will not have that rail available for use. The 5VDC supply from the USB port is provided on the SYS_5V, the one that comes from the TPS65217C, rail of the expansion header for use by a cape. Figure 24 is the connection of the USB power input on the PMIC.

DGND

C1
10uF,10V

U2

TPS65217C

USB

12

C36

0.1uf ,6.3V

DGND | P4 | mini USB-B
| D-
2 | D+

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
DGND
Figure 24. USB Power Connections

### 6.1.4 Power Selection

The selection of either the 5VDC or the USB as the power source is handled internally to the TPS65217C and automatically switches to 5VDC power if both are connected. SW can change the power configuration via the I2C interface from the processor. In addition, the SW can read the TPS65217C and determine if the board is running on the 5VDC input or the USB input. This can be beneficial to know the capability of the board to supply current for things like operating frequency and expansion cards.

It is possible to power the board from the USB input and then connect the DC power supply. The board will switch over automatically to the DC input.

### 6.1.5 Power Button

A power button is connected to the input of the TPS65217C. This is a momentary switch, the same type of switch used for reset and boot selection on the board.

If you push the button the TPS65217C will send an interrupt to the processor. It is up to the processor to then pull the PMIC_EN pin low at the correct time to power down the board. At this point, the PMIC is still active, assuming that the power input was not removed. Pressing the power button will cause the board to power up again if the processor puts the board in the power off mode.

In power off mode, the RTC rail is still active, keeping the RTC powered and running off the main power input. If you remove that power, then the RTC will not be powered. You also have the option of using the battery holes on the board to connect a battery if desired as discussed in the next section.

If you push and hold the button for greater than 8 seconds, the PMIC will power down. But you must release the button when the power LED turns off. Holding the button past that point will cause the board to power cycle.

### 6.1.6 Battery Access Pads

Four pads are provided on the board to allow access to the battery pins on the TPS65217C. The pads can be loaded with a 4x4 header or you may just wire a battery into the pads. In addition they could provide access via a cape if desired. The four signals are listed below in Table 3.

Table 3. | BeagleBone Black Battery Pins
PIN | DESIGNATION | FUNCTION
BAT | TP5 | Battery connection point.
SENSE | TP6 | Battery voltage sense input, connect to BAT directly at the battery terminal.
TS | TP7 | Temperature sense input. Connect to NTC thermistor to sense battery temperature.
GND | TP8 | System ground.

There is no fuel gauge function provide by the TPS65217C. That would need to be added if that function was required. Access to 1-wire SPI, or I2C interfaces required to use a fuel gauge will need to be accessed by using the expansion headers on the board.

## NOTE: Refer to the TPS65217C documentation

before connecting anything to these pins.

### 6.1.7 Power Consumption

The power consumption of the board varies based on power scenarios and the board boot processes. Measurements were taken with the board in the following configuration:

- DC powered and USB powered
- HDMI monitor connected
- USB HUB
- 4GB Thumbdrive
- Ethernet connected @ 100M
- Serial debug cable connected

Table 4 is an analysis of the power consumption of the board in these various scenarios.

Table 4. | BeagleBone Black Power Consumption(mA@5V)
MODE | USB | DC | DC+USB
Reset | TBD | TBD | TBD
Idling @ UBoot | 210 | 210 | 210
Kernel Booting (Peak) | 460 | 460 | 460
Kernel Idling | 350 | 350 | 350
Kernel Idling Display Blank | 280 | 280 | 280
Loading a Webpage | 430 | 430 | 430

The current will fluctuate as various activates occur, such as the LEDs on and uSD/eMMC accesses.

### 6.1.8 Processor Interfaces

The processor interacts with the TPS65217C via several different signals. Each of these signals is described below.

### 6.1.8.1 I2C0

I2C0 is the control interface between the processor and the TPS65217C. It allows the processor to control the registers inside the TPS65217C for such things as voltage scaling and switching of the input rails.

### 6.1.8.2 PMC_POWR_EN

On power up the VDD_RTC rail activates first. After the RTC circuitry in the processor has activated it instructs the TPS65217C to initiate a full power up cycle by activating the PMIC_POWR_EN signal by taking it HI. When powering down, the processor can take this pin low to start the power down process.

### 6.1.8.3 LDO_GOOD

This signal connects to the RTC_PORZn signal, RTC power on reset. As the RTC circuitry comes up first, this signal indicates that the LDOs, the 1.8V VRTC rail, is up and stable. This starts the power up process.

### 6.1.8.4 PMIC_PGOOD

Once all the rails are up, the PMIC_PGOOD signal goes high. This releases the PORZn signal on the processor which was holding the processor reset.

### 6.1.8.5 WAKEUP

The WAKEUP signal from the TPS65217C is connected to the EXT_WAKEUP signal on the processor. This is used to wake up the processor when it is in a sleep mode. When an event is detected by the TPS65217C, such as the power button being pressed, it generates this signal

### 6.1.8.6 PMIC_INT

The PMIC_INT signal is an interrupt signal to the processor. Pressing the power button will send an interrupt to the processor allowing it to implement a power down mode in an orderly fashion, go into sleep mode, or cause it to wake up from a sleep mode. All of these require SW support.

### 6.1.9 Power Rails

Figure 25 shows the connections of each of the rails from the TPS65217C.

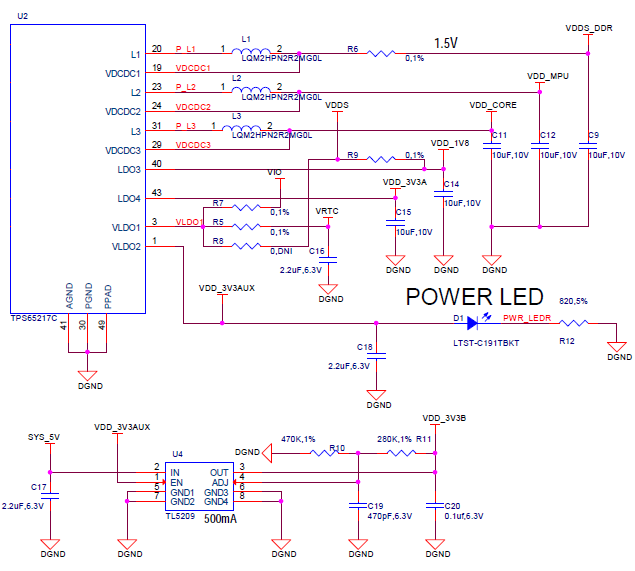
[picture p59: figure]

Figure 25. Power Rails

### 6.1.9.1 VRTC Rail

The VRTC rail is a 1.8V rail that is the first rail to come up in the power sequencing. It provides power to the RTC domain on the processor and the I/O rail of the TPS65217C. It can deliver up to 250mA maximum.

### 6.1.9.2 VDD_3V3A Rail

The VDD_3V3A rail is supplied by the TPS65217C and provides the 3.3V for the processor rails and can provide up to 400mA.

### 6.1.9.3 VDD_3V3B Rail

The current supplied by the VDD_3V3A rail is not sufficient to power all of the 3.3V rails on the board. So a second LDO is supplied, U4, a TL5209A, which sources the VDD_3V3B rail. It is powered up just after the VDD_3V3A rail.

### 6.1.9.4 VDD_1V8 Rail

The VDD_1V8 rail can deliver up to 400mA and provides the power required for the 1.8V rails on the processor and the HDMI framer. This rail is not accessible for use anywhere else on the board.

### 6.1.9.5 VDD_CORE Rail

The VDD_CORE rail can deliver up to 1.2A at 1.1V. This rail is not accessible for use anywhere else on the board and only connects to the processor. This rail is fixed at 1.1V and is not scaled.

### 6.1.9.6 VDD_MPU Rail

The VDD_MPU rail can deliver up to 1.2A. This rail is not accessible for use anywhere else on the board and only connects to the processor. This rail defaults to 1.1V and can be scaled up to allow for higher frequency operation. Changing of the voltage is set via the I2C interface from the processor.

### 6.1.9.7 VDDS_DDR Rail

The VDDS_DDR rail defaults to 1.5V to support the DDR3L rails and can deliver up to 1.2A. It is possible to adjust this voltage rail down to 1.35V for lower power operation of the DDR3L device. Only DDR3L devices can support this voltage setting of 1.35V.

### 6.1.9.8 Power Sequencing

The power up process is made up of several stages and events. Figure 26 describes the events that make up the power up process for the processer.

Figure 26. Power Rail Power Up Sequencing

Figure 27 the voltage rail sequencing for the TPS65217C as it powers up and the voltages on each rail. The power sequencing starts at 15 and then goes to one. That is the way the TPS65217C is configured. You can refer to the TPS65217C datasheet for more information.

Figure 27. TPS6517C Power Sequencing Timing

### 6.1.10 Power LED

The power LED is a blue LED that will turn on once the TPS65217C has finished the power up procedure. If you ever see the LED flash once, that means that the TPS65217C started the process and encountered an issue that caused it to shut down. The connection of the LED is shown in Figure 25.

### 6.1.11 TPS65217C Power Up Process

Figure 14 shows the interface between the TPS65217C and the processor.

Figure 28. Power Processor Interfaces

When voltage is applied, DC or USB, the TPS65217C connects the power to the SYS output pin which drives the switchers and LDOS in the TPS65217C.

At power up all switchers and LDOs are off except for the VRTC LDO (1.8V), which provides power to the VRTC rail and controls the RTC_PORZ input pin to the processor, which starts the power up process of the processor. Once the RTC rail powers up, the RTC_PORZ pin of the processor is released.

Once the RTC_PORZ reset is released, the processor starts the initialization process. After the RTC stabilizes, the processor launches the rest of the power up process by activating the PMIC_PWR_EN signal that is connected to the TPS65217C which starts the TPS65217C power up process.

The LDO_PGOOD signal is provided by the TPS65217C to the processor. As this signal is 1.8V from the TPS65217C by virtue of the TPS65217C VIO rail being set to 1.8V, and the RTC_PORZ signal on the processor is 3.3V, a voltage level shifter, U4, is used. Once the LDOs and switchers are up on the TPS65217C, this signal goes active releasing the processor. The LDOs on the TPS65217C are used to power the VRTC rail on the processor.

### 6.1.12 Processor Control Interface

Figure 11 above shows two interfaces between the processor and the TPS65217C used for control after the power up sequence has completed.

The first is the I2C0 bus. This allows the processor to turn on and off rails and to set the voltage levels of each regulator to supports such things as voltage scaling.

The second is the interrupt signal. This allows the TPS65217C to alert the processor when there is an event, such as when the optional power button is pressed. The interrupt is an open drain output which makes it easy to interface to 3.3V of the processor.

### 6.1.13 Low Power Mode Support

This section covers three general power down modes that are available. These modes are only described from a Hardware perspective as it relates to the HW design.

### 6.1.13.1 RTC Only

In this mode all rails are turned off except the VDD_RTC. The processor will need to turn off all the rails to enter this mode. The VDD_RTC staying on will keep the RTC active and provide for the wakeup interfaces to be active to respond to a wake up event.

### 6.1.13.2 RTC Plus DDR

In this mode all rails are turned off except the VDD_RTC and the VDDS_DDR, which powers the DDR3L memory. The processor will need to turn off all the rails to enter this mode. The VDD_RTC staying on will keep the RTC active and provide for the wakeup interfaces to be active to respond to a wake up event.

The VDDS_DDR rail to the DDR3L is provided by the 1.5V rail of the TPS65217C and with VDDS_DDR active, the DDR3L can be placed in a self refresh mode by the processor prior to power down which allows the memory data to be saved.

Currently, this feature is not included in the standard software release. The plan is to include it in future releases.

### 6.1.13.3 Voltage Scaling

For a mode where the lowest power is possible without going to sleep, this mode allows the voltage on the ARM processor to be lowered along with slowing the processor frequency down. The I2C0 bus is used to control the voltage scaling function in the TPS65217C.

### 6.2 Sitara XAM3359AZCZ100 Processor

The board is designed to use either the Sitara AM3358AZCZ100 or XAM3358BZCZ100 processor in the 15 x 15 package. The initial units built will use the XAM3359AZCZ100 processor from TI. This is the same processor as used on the original BeagleBone except for a different revision. Later, we will switch to the AM3358BZCZ100 device when released.

### 6.2.1 Description

Figure 29 is a high level block diagram of the processor. For more information on the processor, go to http://www.ti.com/product/am3359.

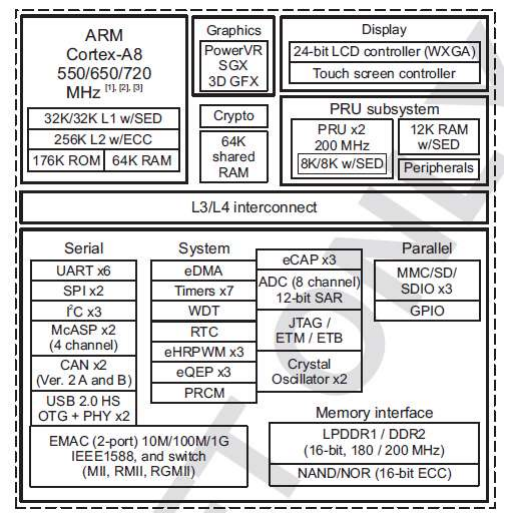
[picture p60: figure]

Figure 29. Sitara XAM3359AZCZ Block Diagram

NOTE: Figure 29 is an older block diagram and the higher frequency is not reflected. As soon an updated picture is available, this will be changed. You can also refer to the updated datasheet for the XAM3359 processor.

### 6.2.2 High Level Features

Table 5 below shows a few of the high level features of the Sitara processor.

Table 5. | Processor Features
Operating Systems | Linux, Android, Windows Embedded CE,QNX, ThreadX | MMC/SD | 3
Standby Power | 7 mW | CAN | 2
ARM CPU | 1 ARM Cortex-A8 | UART (SCI) | 6
ARM MHz (Max.) | 275,500,600,800,1000 | ADC | 8-ch 12-bit
ARM MIPS (Max.) | 1000,1200,2000 | PWM (Ch) | 3
Graphics Acceleration | 1 3D | eCAP | 3
Other Hardware Acceleration | 2 PRU-ICSS,Crypto Accelerator | eQEP | 3
On-Chip L1 Cache | 64 KB (ARM Cortex-A8) | RTC | 1
On-Chip L2 Cache | 256 KB (ARM Cortex-A8) | I2C | 3
Other On-Chip Memory | 128 KB | McASP | 2
Display Options | LCD | SPI | 2
General Purpose Memory | 1 16-bit (GPMC, NAND flash, NOR Flash, SRAM) | DMA (Ch) | 64-Ch EDMA
DRAM | DDR2-532, DDR3-606) 1 16-bit (LPDDR-400, | IO Supply (V) | 1.8V(ADC),3.3V
USB Ports | 2 | Operating Temperature Range (C) | -40 to 90

### 6.2.3 Documentation

Full documentation for the processor can be found on the TI website at http://www.ti.com/product/am3359 for the current processor used on the board. Make sure that you always use the latest datasheets and Technical Reference Manuals (TRM).

### 6.3 DDR3L Memory

The BeagleBone Black uses a single MT41K256M16HA-125 512MB DDR3L device from Micron that interfaces to the processor over 16 data lines, 16 address lines, and 14 control lines. The following sections provide more details on the design.

### 6.3.1 Memory Device

The design will support standard DDR3 and DDR3L x16 devices. A single x16 device is used on the board and there is no support for two x8 devices. The DDR3 devices work at 1.5V and the DDR3L devices can work down to 1.35V to achieve lower power. The specific Micron device used is the MT41K256M16HA-125. It comes in a 96-BALL FBGA package with 0.8 mil pitch. Other standard DDR3 devices can also be supported, but the DDR3L is the lower power device and was chosen for its ability to work at 1.5V or 1.35V. The standard frequency that the DDR3L is run at on the board is 303MHZ.

### 6.3.2 DDR3L Memory Design

Figure 30 is the schematic for the DDR3L memory device. Each of the groups of signals is described in the following lines.

Address Lines: Provide the row address for ACTIVATE commands, and the column address and auto pre-charge bit (A10) for READ/WRITE commands, to select one location out of the memory array in the respective bank. A10 sampled during a PRECHARGE command determines whether the PRECHARGE applies to one bank (A10 LOW, bank selected by BA[2:0]) or all banks (A10 HIGH). The address inputs also provide the op-code during a LOAD MODE command. Address inputs are referenced to VREFCA. A12/BC#: When enabled in the mode register (MR), A12 is sampled during READ and WRITE commands to determine whether burst chop (on-the-fly) will be performed (HIGH = BL8 or no burst chop, LOW = BC4 burst chop).

Bank Address Lines: BA[2:0] define the bank to which an ACTIVATE, READ, WRITE, or PRECHARGE command is being applied. BA[2:0] define which mode register (MR0, MR1, MR2, or MR3) is loaded during the LOAD MODE command. BA[2:0] are referenced to VREFCA.

CK and CK# Lines: are differential clock inputs. All address and control input signals are sampled on the crossing of the positive edge of CK and the negative edge of CK#. Output data strobe (DQS, DQS#) is referenced to the crossings of CK and CK#.

Clock Enable Line: CKE enables (registered HIGH) and disables (registered LOW) internal circuitry and clocks on the DRAM. The specific circuitry that is enabled/disabled is dependent upon the DDR3 SDRAM configuration and operating mode. Taking CKE LOW provides PRECHARGE power-down and SELF REFRESH operations (all banks idle) or active power-down (row active in any bank). CKE is synchronous for power-down entry and exit and for self refresh entry. CKE is asynchronous for self refresh exit.

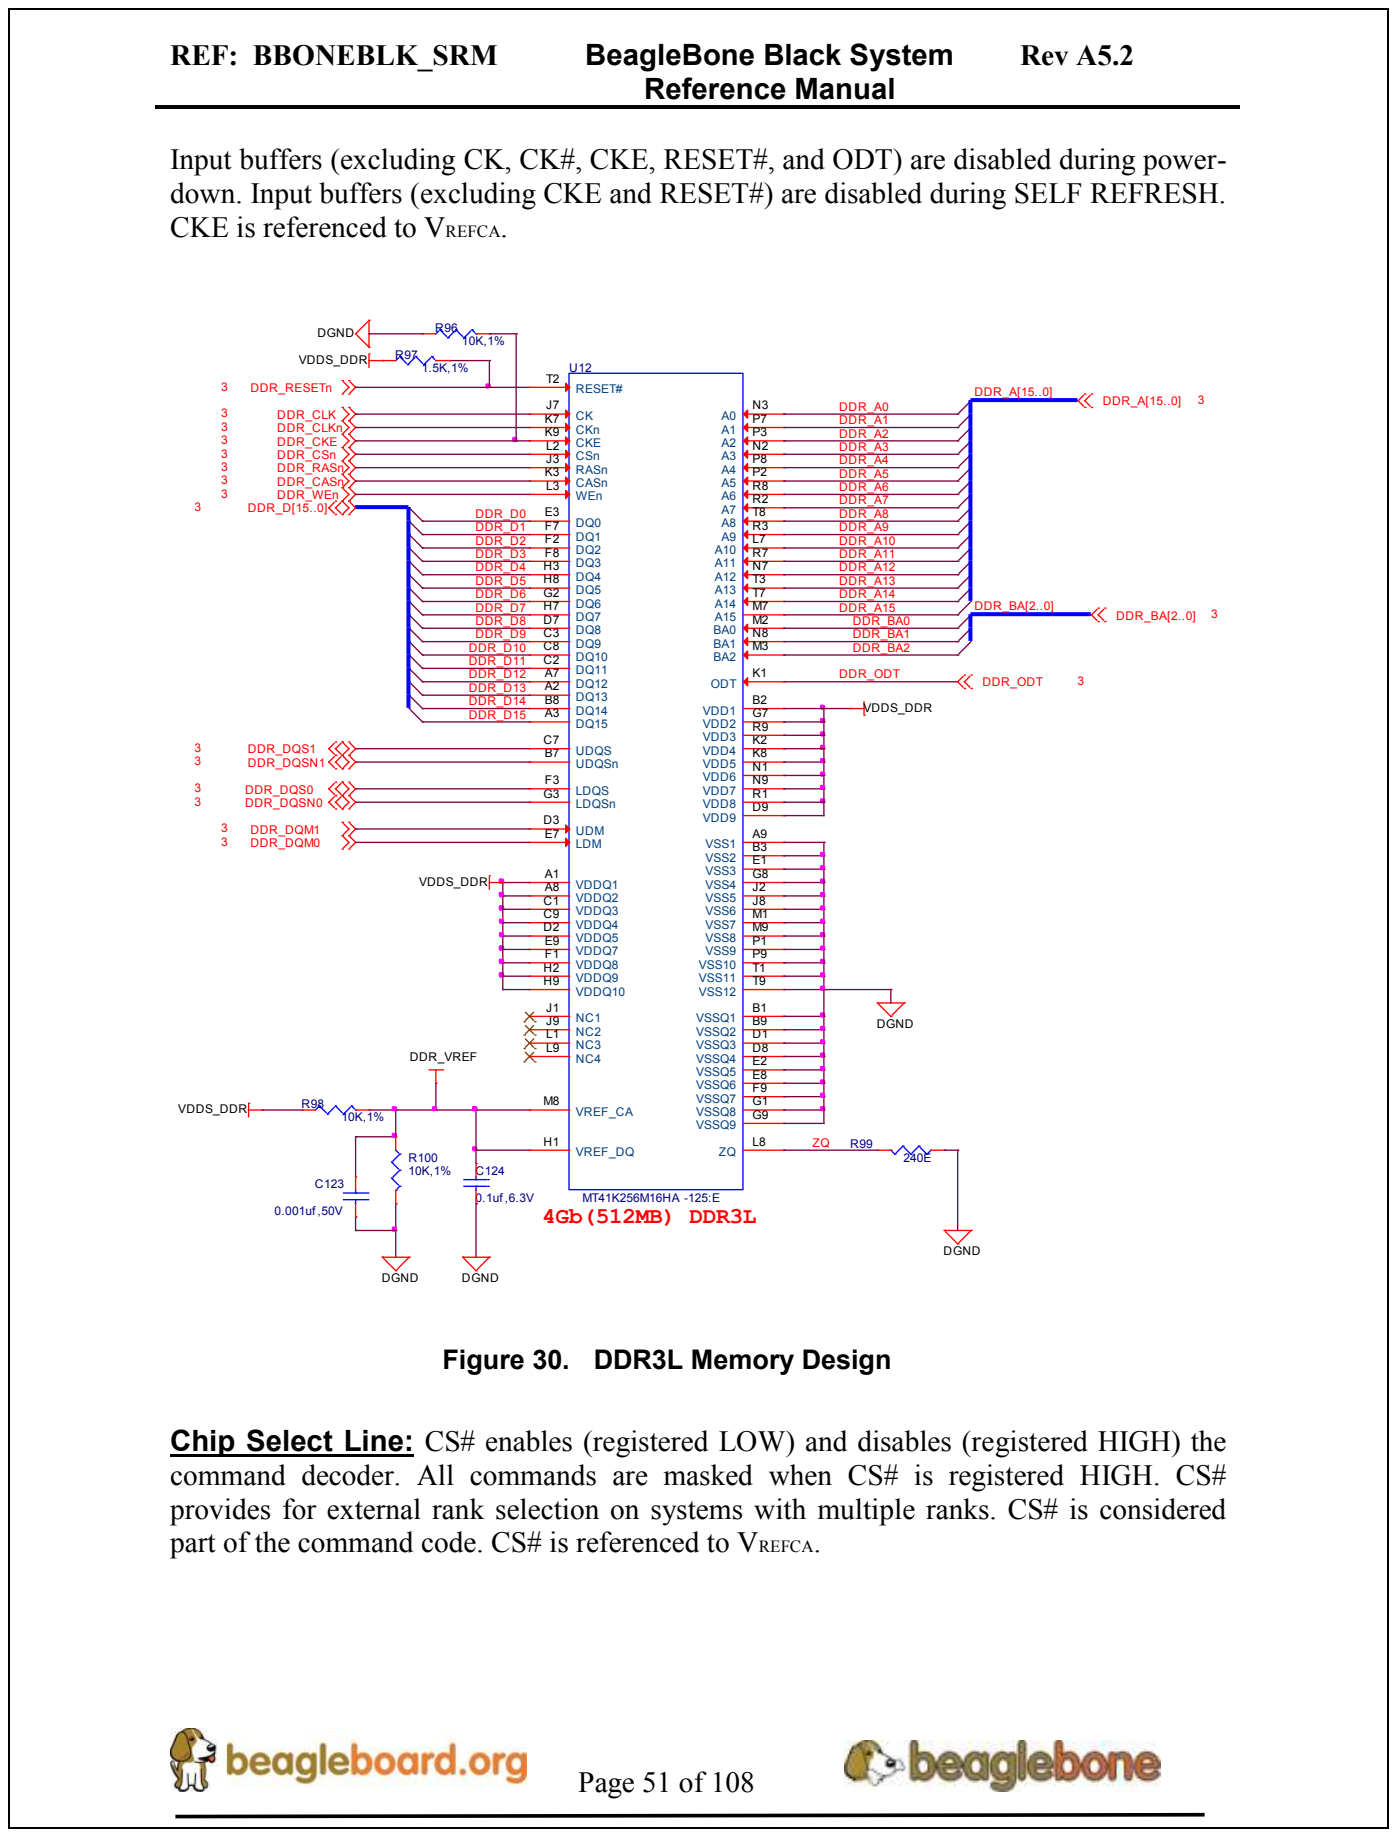
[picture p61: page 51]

Input buffers (excluding CK, CK#, CKE, RESET#, and ODT) are disabled during power-
down. Input buffers (excluding CKE and RESET#) are disabled during SELF REFRESH.
CKE is referenced to VREFCA.

Chip Select Line: CS# enables (registered LOW) and disables (registered HIGH) the
command decoder. All commands are masked when CS# is registered HIGH. CS#
provides for external rank selection on systems with multiple ranks. CS# is considered
part of the command code. CS# is referenced to VREFCA.

Input Data Mask Line: DM is an input mask signal for write data. Input data is masked when DM is sampled HIGH along with the input data during a write access. Although the DM ball is input-only, the DM loading is designed to match that of the DQ and DQS balls. DM is referenced to VREFDQ.

On-die Termination Line: ODT enables (registered HIGH) and disables (registered LOW) termination resistance internal to the DDR3L SDRAM. When enabled in normal operation, ODT is only applied to each of the following balls: DQ[7:0], DQS, DQS#, and DM for the x8; DQ[3:0], DQS, DQS#, and DM for the x4. The ODT input is ignored if disabled via the LOAD MODE command. ODT is referenced to VREFCA.

### 6.3.3 Power Rails

The DDR3L memory device and the DDR3 rails on the processor are supplied by the TPS65217C. Default voltage is 1.5V but can be scaled down to 1.35V if desired.

### 6.3.4 VREF

The VREF signal is generated from a voltage divider on the VDDS_DDR rail that powers the processor DDR rail and the DDR3L device itself. Figure 31 below shows the configuration of this signal and the connection to the DDR3L memory device and the processor.

U12

MT41K256M16HA-125

VREF_DQ

H1

VREF_CA

M8

15mm x 15mm
Package

U5A

XAM3359AZCZ

VREFSSTL

J4

C124

0.1uf ,6.3V

R100
10K,1%

R98
10K,1%

C123

0.001uf ,50V

DGND

DDR_VREF

VDDS_DDR

DGND

DGND

C28

0.1uf ,6.3V

DDR_VREF

Figure 31. DDR3L VREF Design

6.4 2GB eMMC Memory

The eMMC is a communication and mass data storage device that includes a Multi-MediaCard (MMC) interface, a NAND Flash component, and a controller on an advanced 11-signal bus, which is compliant with the MMC system specification. The nonvolatile eMMC draws no power to maintain stored data, delivers high performance across a wide range of operating temperatures, and resists shock and vibration disruption.

One of the issues faced with SD cards is that across the different brands and even within the same brand, performance can vary. Cards use different controllers and different memories, all of which can have bad locations that the controller handles. But the controllers may be optimized for reads or writes. You never know what you will be getting. This can lead to varying rates of performance. The eMMC card is a known controller and when coupled with the 8bit mode, 8 bits of data instead of 4, you get double the performance which should result in quicker boot times.

The following sections describe the design and device that is used on the board to implement this interface.

### 6.4.1 eMMC Device

The device used in a Micron MTFC2GMTEA-0F_WT 2GB eMMC device. This is a new device and so for documentation and support, you will need to contact your local Micron representative.

The package is a 153 ball WFBGA device. The footprint on the BeagleBone Black for this device supports 4GB and 8GB devices. As this is a JEDEC standard, there are other suppliers that may work in this design as well. The only device that has been tested is the MTFC2GMTEA-0F_WT.

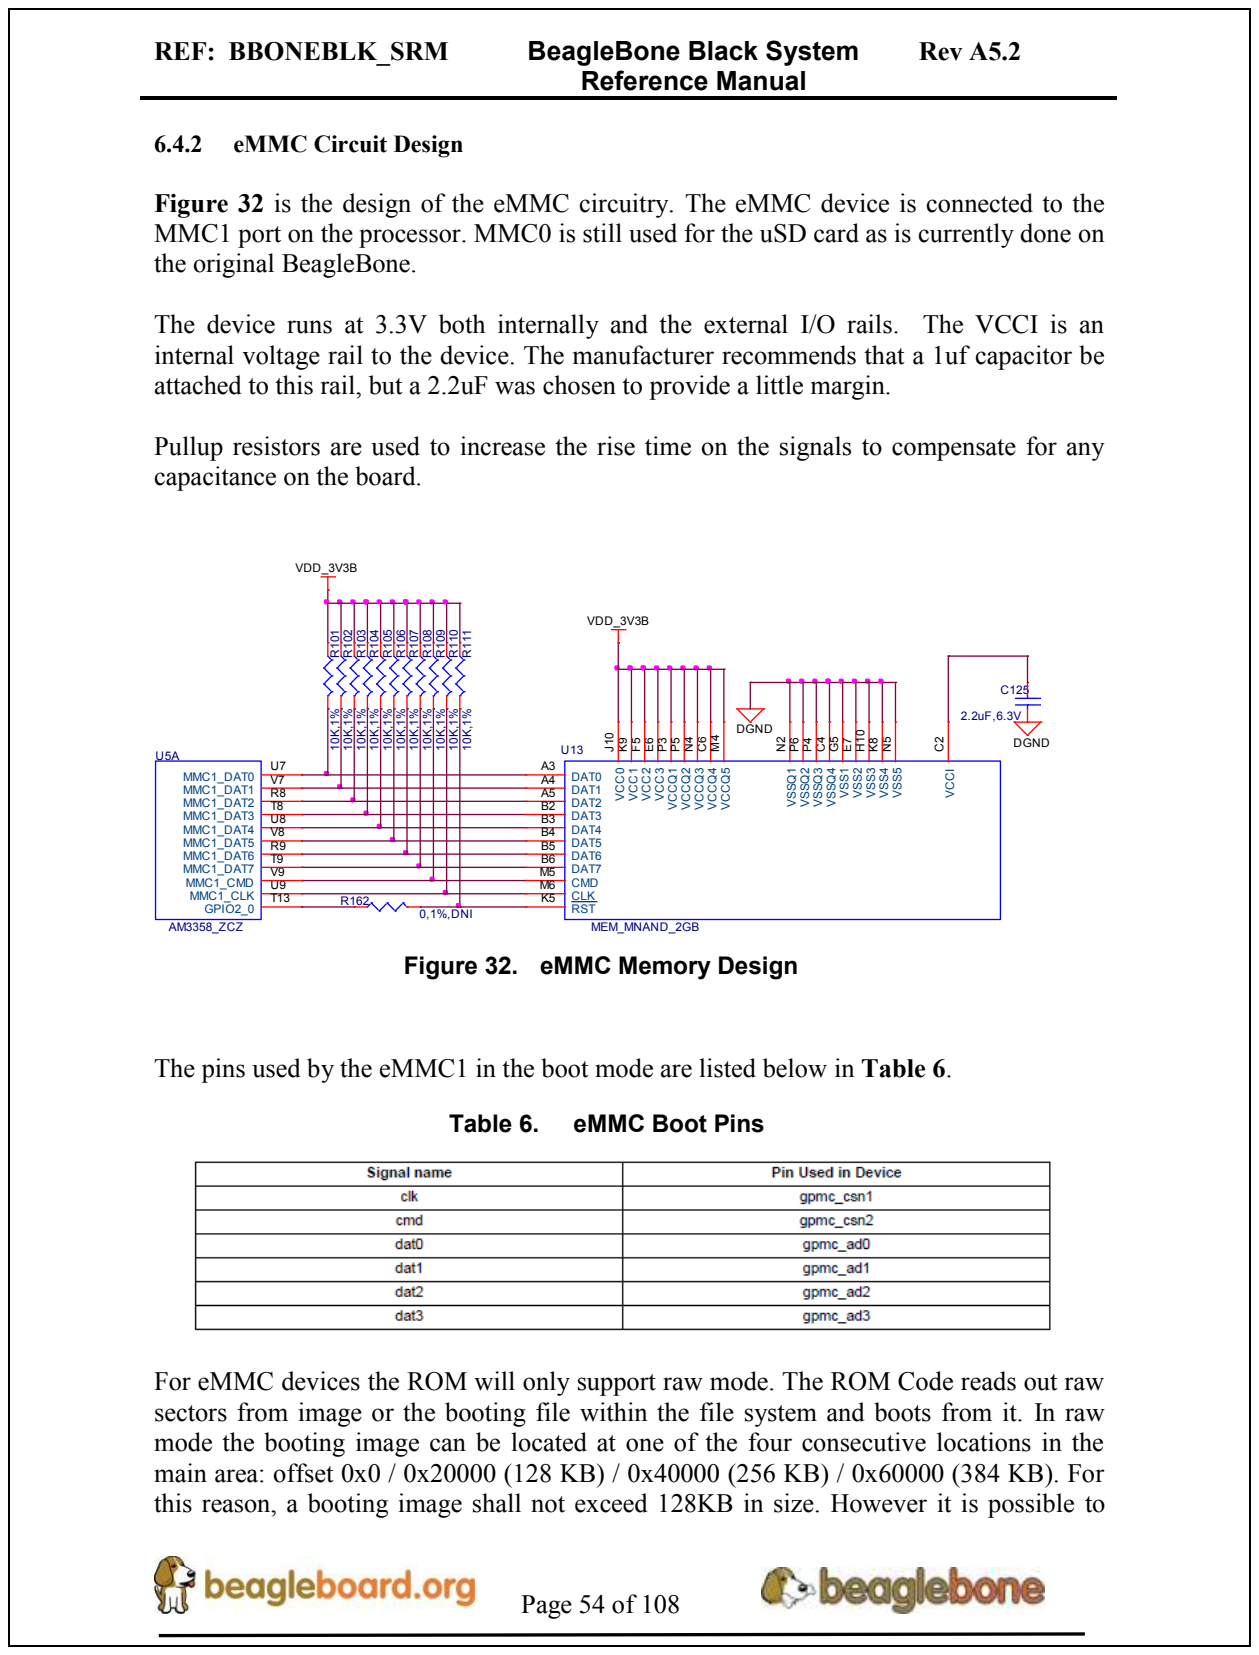
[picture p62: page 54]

Figure 32 is the design of the eMMC circuitry. The eMMC device is connected to the
MMC1 port on the processor. MMC0 is still used for the uSD card as is currently done on
the original BeagleBone.

The device runs at 3.3V both internally and the external I/O rails. The VCCI is an
internal voltage rail to the device. The manufacturer recommends that a 1uf capacitor be
attached to this rail, but a 2.2uF was chosen to provide a little margin.

Pullup resistors are used to increase the rise time on the signals to compensate for any
capacitance on the board.

Figure 32. eMMC Memory Design

The pins used by the eMMC1 in the boot mode are listed below in Table 6.

For eMMC devices the ROM will only support raw mode. The ROM Code reads out raw
sectors from image or the booting file within the file system and boots from it. In raw
mode the booting image can be located at one of the four consecutive locations in the
main area: offset 0x0 / 0x20000 (128 KB) / 0x40000 (256 KB) / 0x60000 (384 KB). For
this reason, a booting image shall not exceed 128KB in size. However it is possible to

flash a device with an image greater than 128KB starting at one of the aforementioned locations. Therefore the ROM Code does not check the image size. The only drawback is that the image will cross the subsequent image boundary. The raw mode is detected by reading sectors #0, #256, #512, #768. The content of these sectors is then verified for presence of a TOC structure. In the case of a GP Device, a Configuration Header (CH) must be located in the first sector followed by a GP header. The CH might be void (only containing a CHSETTINGS item for which the Valid field is zero).

The ROM only supports the 4-bit mode. After the initial boot, the switch can be made to 8-bit mode for increasing the overall performance of the eMMC interface.

### 6.5 Micro Secure Digital

The uSD connector on the board will support a uSD card that can be used for booting or file storage on the BeagleBone Black.

### 6.5.1 uSD Design

Figure 33 below is the design of the uSD interface on the board.

U5A

AM3358_ZCZ

MMC0_CLK

G17

MMC0_CMD

G18

MMC0_DAT0

G16

MMC0_DAT1

G15

MMC0_DAT2

F18

MMC0_DAT3

F17

MMC0_SDCD

C15

DGND

SD_CD

DGND R¹⁵⁰ 10K,1% | R¹⁵³ 10K,1% R¹⁵¹ 10K,1%
R157 | 10K,1% R¹⁵² 10K,1% | R¹⁵⁴ 10K,1% | R¹⁵⁵ 10K,1%

VDD_3V3B

VDD_3V3B

DGND

C153

10uF,10V

microSD

P7

MOLEX 502570-001

DAT2

1

CD/DAT3

2

CMD

3

VDD

4

CLOCK

5

VSS

6

DAT0

7

DAT1

8

GND

9

GND1

10

CD

11

GND2

12

GND3

13

GND4

14

C154

0.1uf ,6.3V

Figure 33. uSD Design

The signals MMC0-3 are the data lines for the transfer of data between the processor and the uSD connector.

The MMC0_CLK signal clocks the data in and out of the uSD card.

The MMCO_CMD signal indicates that a command versus data is being sent.

There is no separate card detect pin in the uSD specification. It uses MMCO_DAT3 for that function. However, most uSD connectors still supply a CD function on the

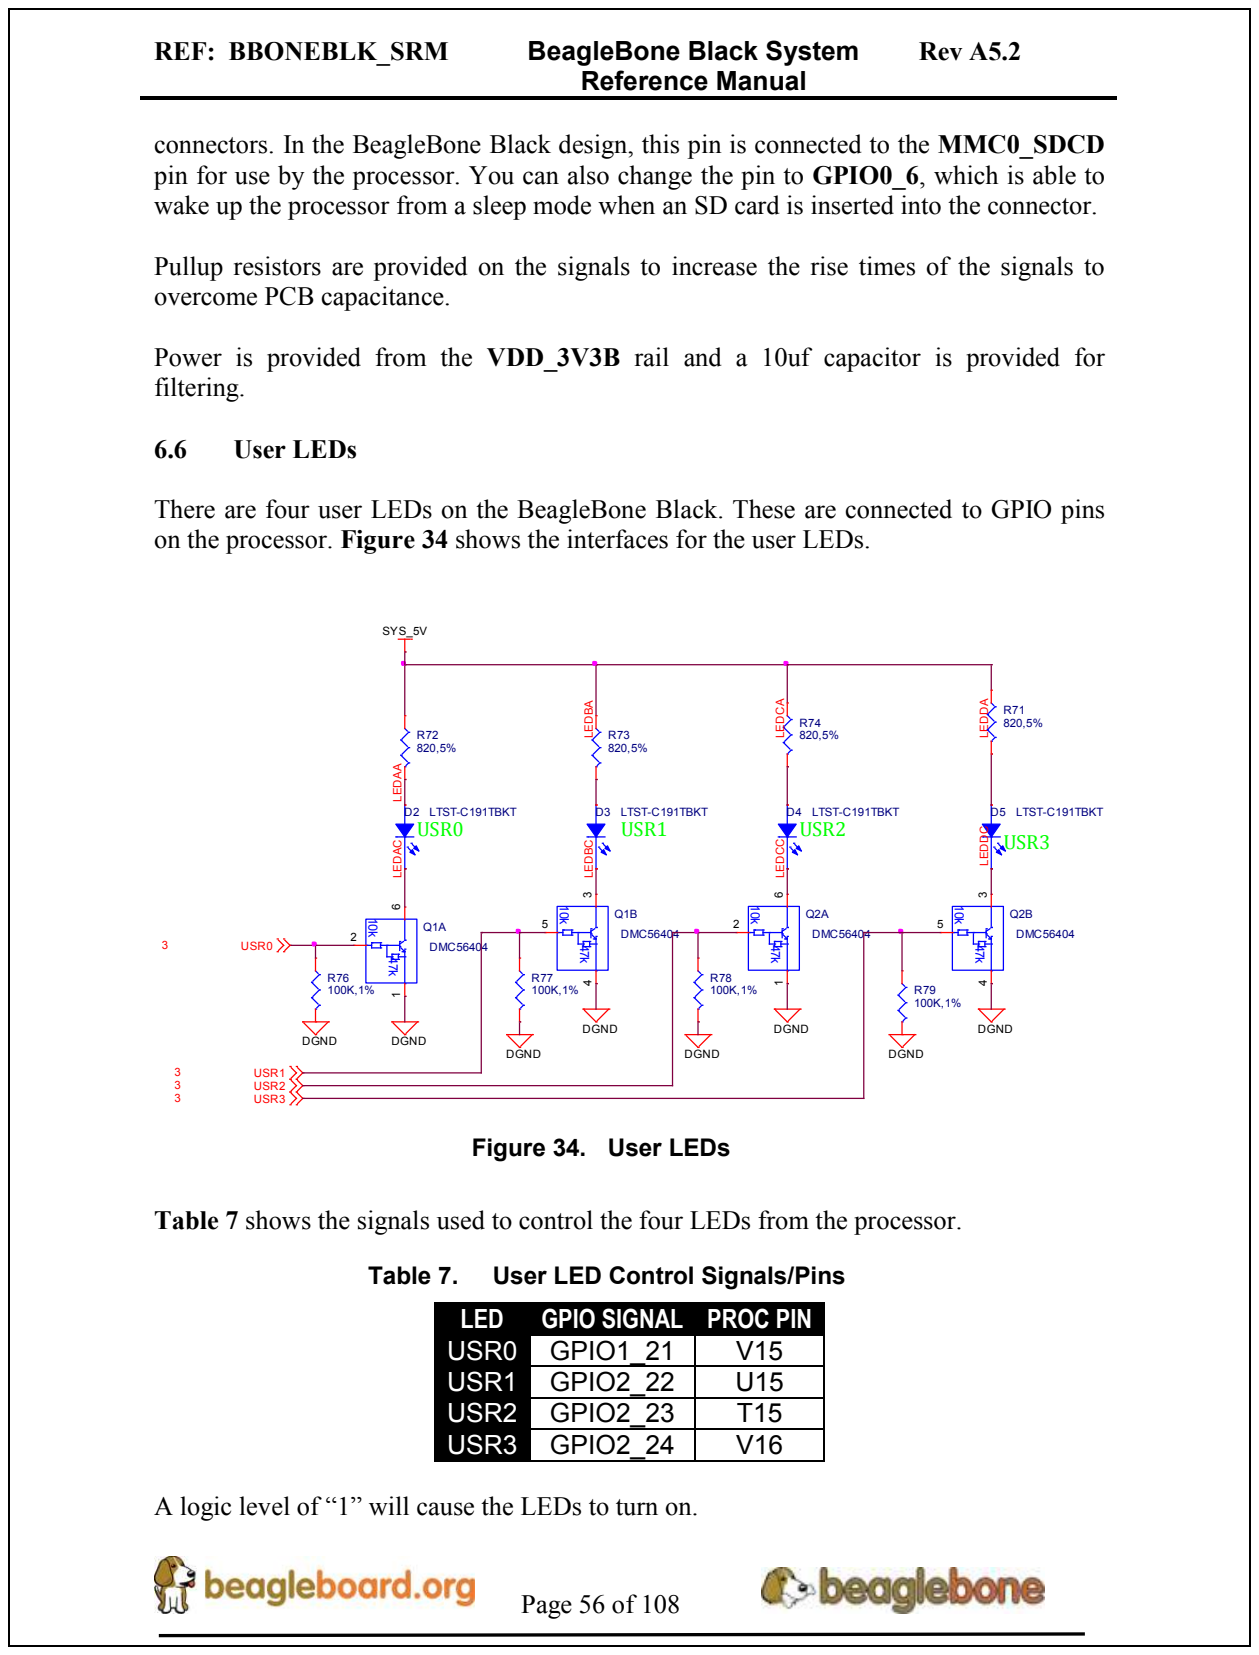
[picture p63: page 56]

connectors. In the BeagleBone Black design, this pin is connected to the MMC0_SDCD
pin for use by the processor. You can also change the pin to GPIO0_6, which is able to
wake up the processor from a sleep mode when an SD card is inserted into the connector.

Pullup resistors are provided on the signals to increase the rise times of the signals to
overcome PCB capacitance.

Power is provided from the VDD_3V3B rail and a 10uf capacitor is provided for
filtering.

There are four user LEDs on the BeagleBone Black. These are connected to GPIO pins
on the processor. Figure 34 shows the interfaces for the user LEDs.

Table 7 shows the signals used to control the four LEDs from the processor.

LED | GPIO SIGNAL | PROC PIN
USR0 | GPIO1_21 | V15
USR1 | GPIO2_22 | U15
USR2 | GPIO2_23 | T15
USR3 | GPIO2_24 | V16

A logic level of “1” will cause the LEDs to turn on.

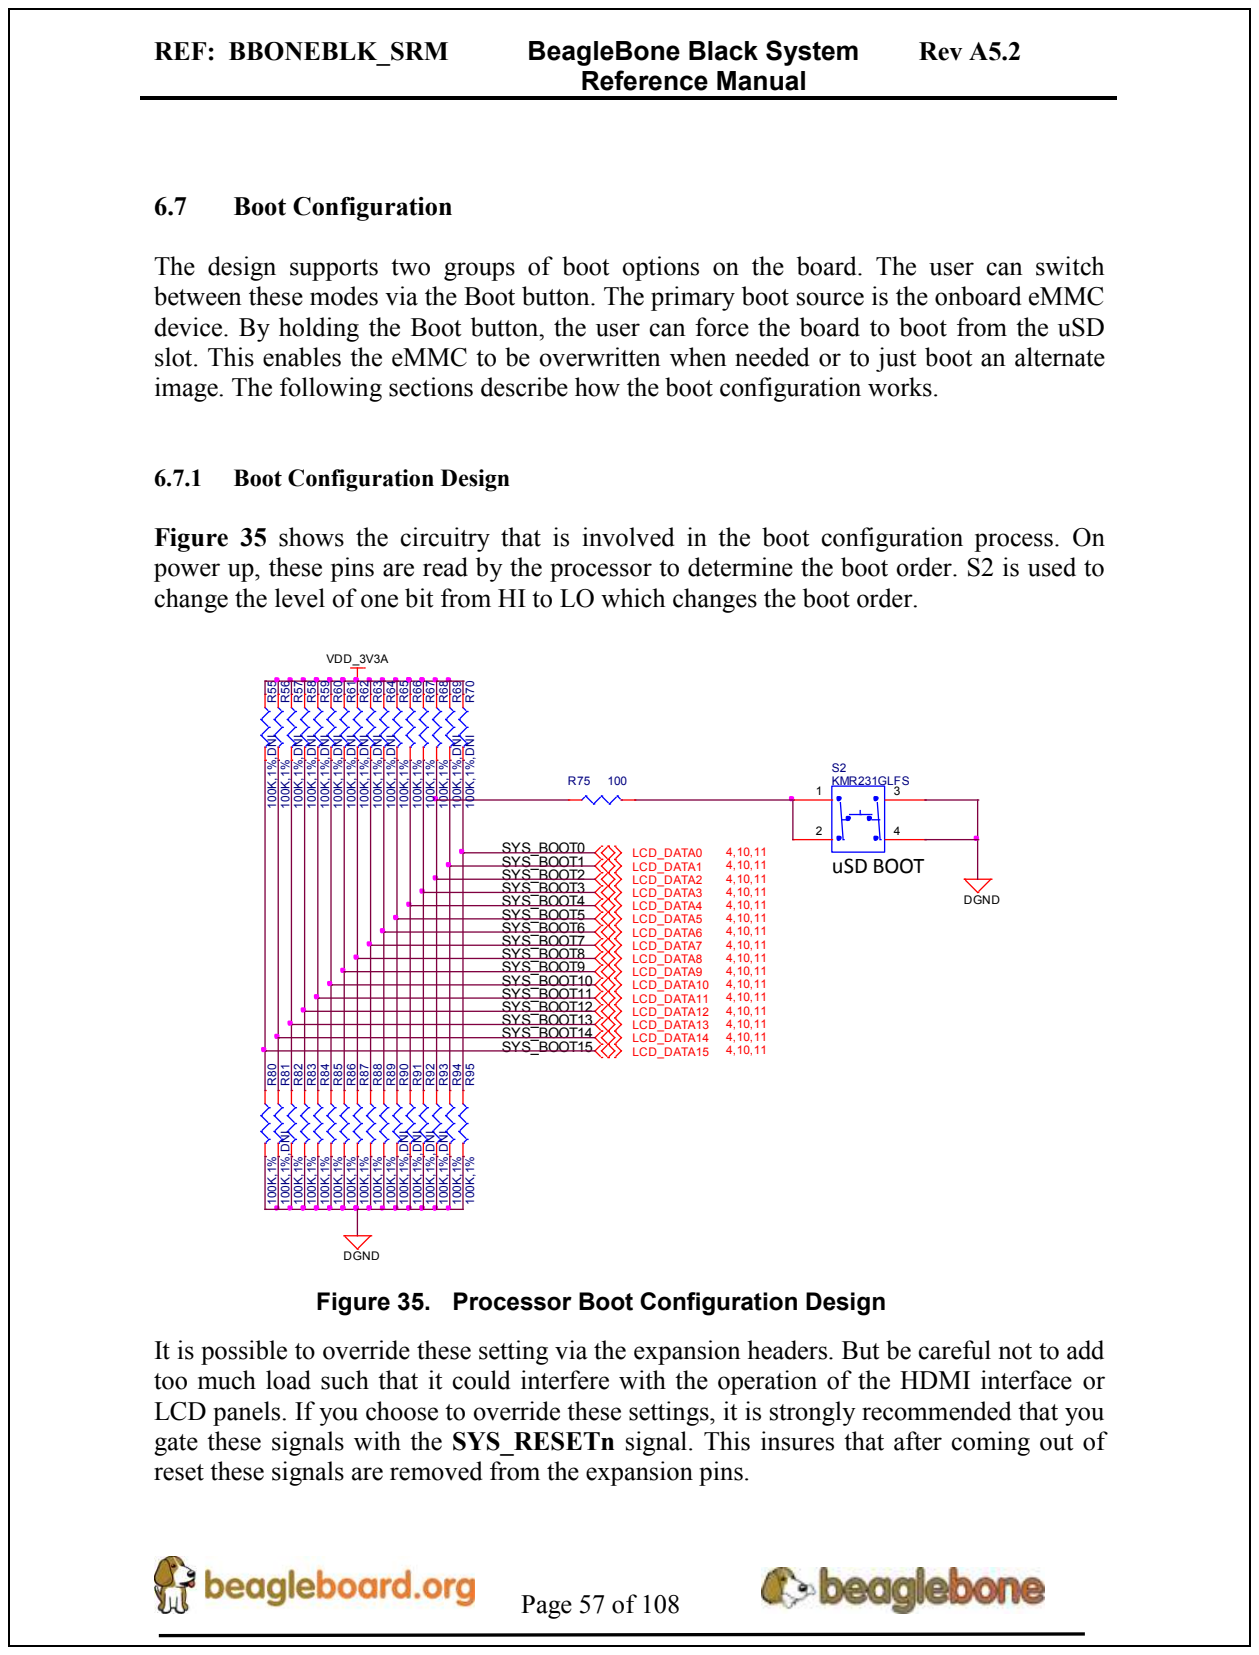
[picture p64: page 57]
6.7 Boot Configuration; change the level of one bit from HI to LO which changes the boot order. R⁸⁰ 100K,1%; R⁸³ 100K,1% R⁸⁴ 100K,1% R⁸⁵ 100K,1%; R⁸⁷ 100K,1% R⁸⁶ 100K,1%; R⁸⁹ 100K,1% R⁸⁸ 100K,1% R⁸² 100K,1%; R⁹⁵ 100K,1%; uSD BOOT; VDD_3V3A; SYS_BOOT10; SYS_BOOT9; SYS_BOOT8; SYS_BOOT15; SYS_BOOT14; SYS_BOOT13; SYS_BOOT12; SYS_BOOT11; SYS_BOOT4; SYS_BOOT2; SYS_BOOT1; SYS_BOOT0; SYS_BOOT7; SYS_BOOT6; SYS_BOOT5; SYS_BOOT3; LCD_DATA5; LCD_DATA4; LCD_DATA3; 4,10,11 R⁶⁵ 100K,1%; LCD_DATA8; LCD_DATA7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

The design supports two groups of boot options on the board. The user can switch
between these modes via the Boot button. The primary boot source is the onboard eMMC
device. By holding the Boot button, the user can force the board to boot from the uSD
slot. This enables the eMMC to be overwritten when needed or to just boot an alternate
image. The following sections describe how the boot configuration works.

6.7.1 Boot Configuration Design

Figure 35 shows the circuitry that is involved in the boot configuration process. On
power up, these pins are read by the processor to determine the boot order. S2 is used to

DGND R⁹⁰ 100K,1%,DNI R⁶⁴ 100K,1%,DNI

DGND
Figure 35. Processor Boot Configuration Design

It is possible to override these setting via the expansion headers. But be careful not to add
too much load such that it could interfere with the operation of the HDMI interface or
LCD panels. If you choose to override these settings, it is strongly recommended that you
gate these signals with the SYS_RESETn signal. This insures that after coming out of
reset these signals are removed from the expansion pins.

### 6.7.2 Default Boot Options

Based on the selected option found in Figure 36 below, each of the boot sequences for each of the two settings is shown.

Figure 36. Processor Boot Configuration

The first row in Figure 36 is the default setting. On boot, the processor will look for the eMMC on the MMC1 port first, followed by the uSD slot on MMC0, USB0 and UART0. In the event there is no uSD card and the eMMC is empty, UART0 or USB0 could be used as the board source.

If you have a uSD card from which you need to boot from, hold the boot button down. On boot, the processor will look for the SPIO0 port first, then uSD on the MMC0 port, followed by USB0 and UART0. In the event there is no uSD card and the eMMC is empty, USB0 or UART0 could be used as the board source.

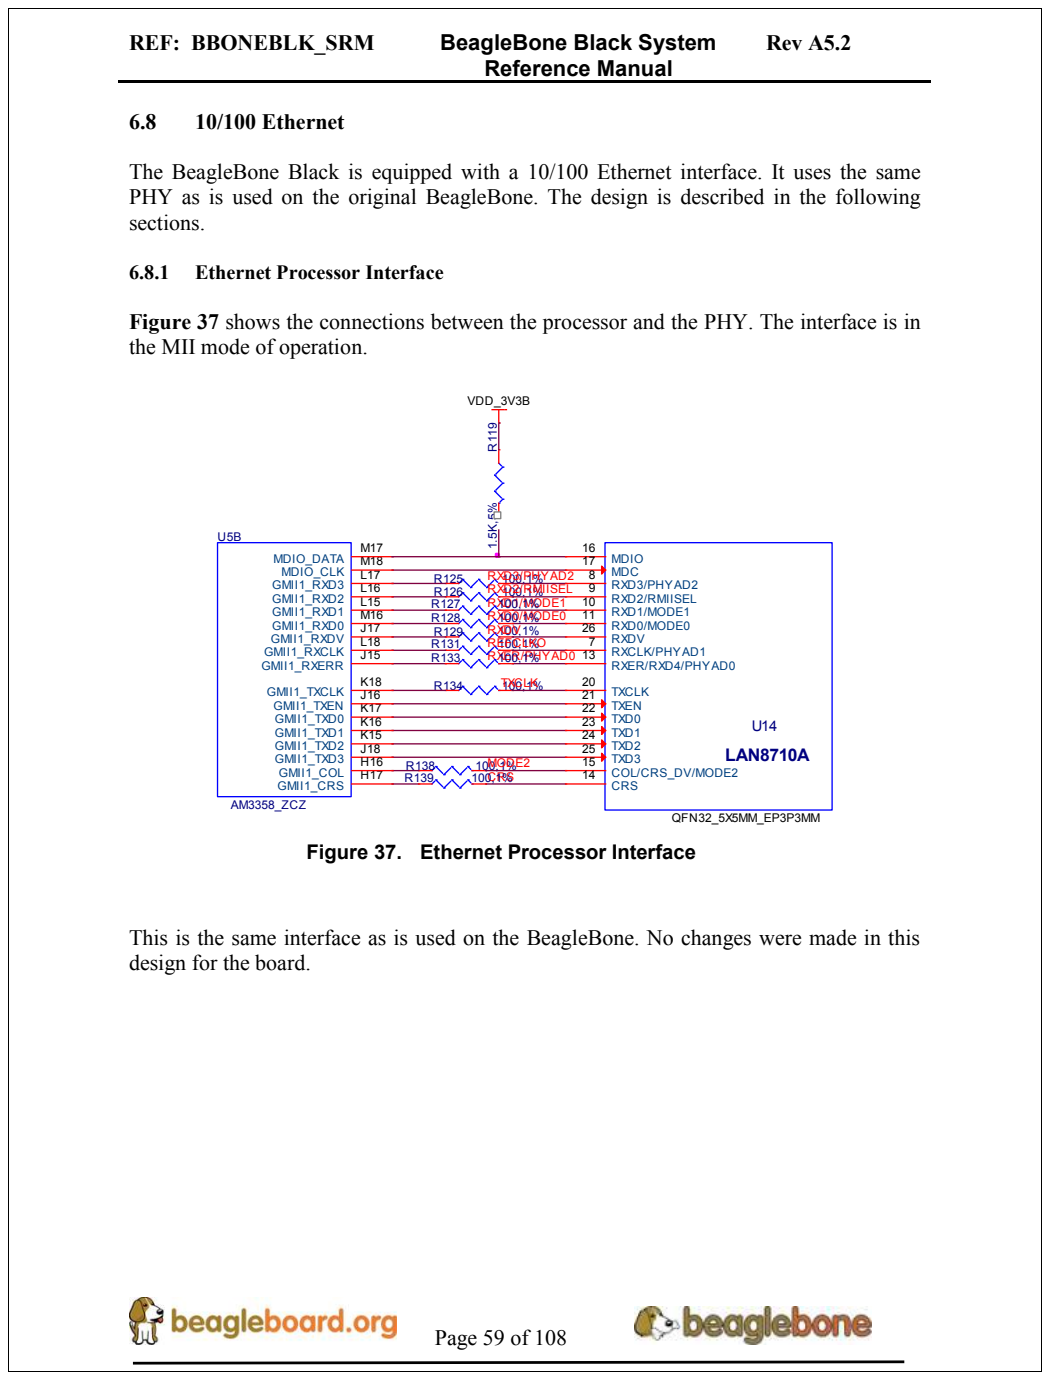
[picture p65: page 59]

The BeagleBone Black is equipped with a 10/100 Ethernet interface. It uses the same
PHY as is used on the original BeagleBone. The design is described in the following
sections.

Figure 37 shows the connections between the processor and the PHY. The interface is in
the MII mode of operation.

Figure 37. Ethernet Processor Interface

This is the same interface as is used on the BeagleBone. No changes were made in this
design for the board.

# 10K,1% R¹²⁰ 49.9,1%

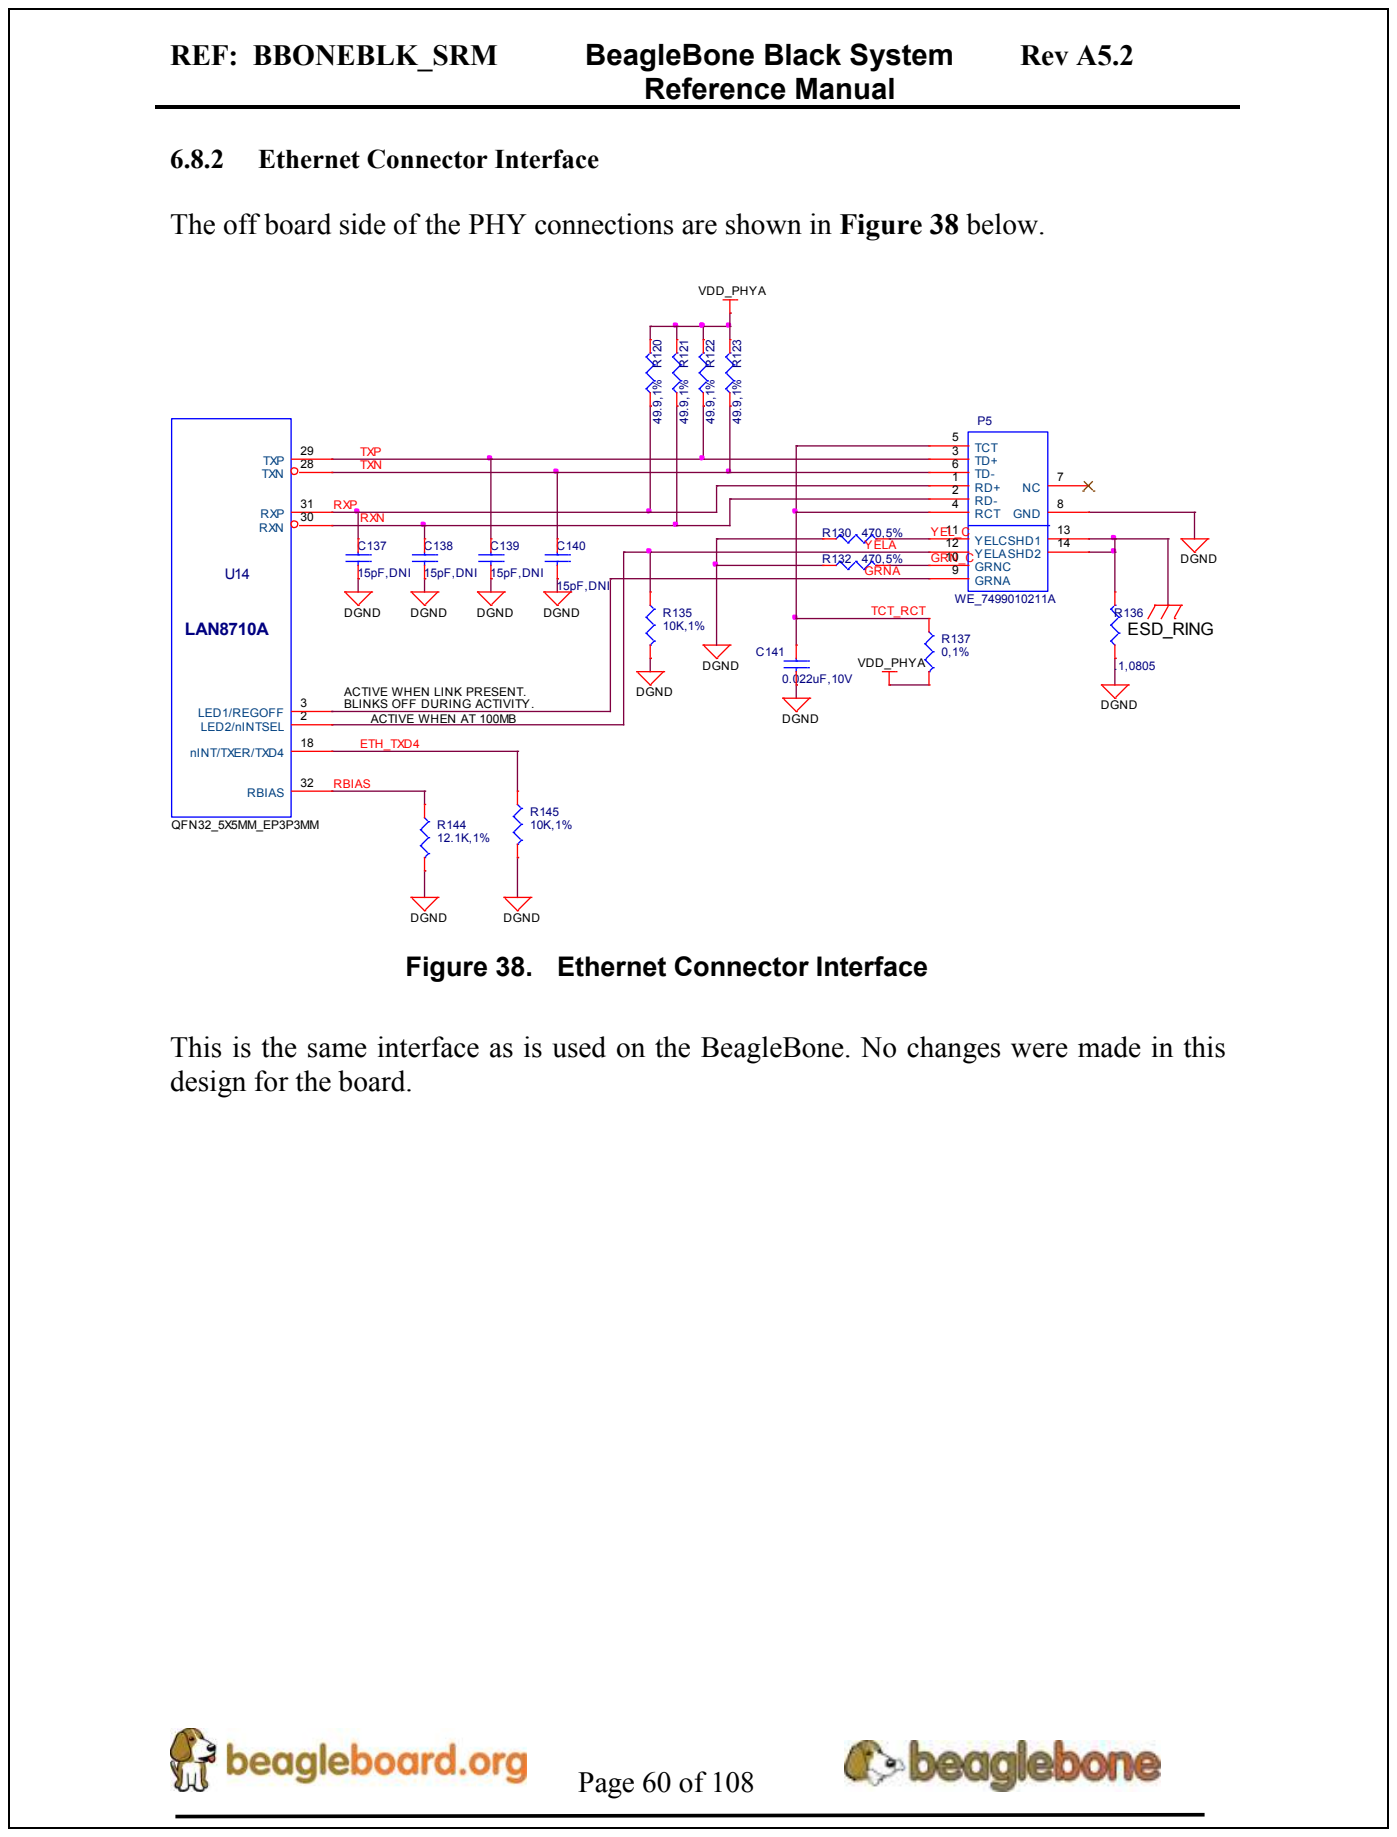
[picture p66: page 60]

The off board side of the PHY connections are shown in Figure 38 below.

ACTIVE WHEN LINK PRESENT.
BLINKS OFF DURING ACTIVITY.
ACTIVE WHEN AT 100MB

DGND
Figure 38. Ethernet Connector Interface

This is the same interface as is used on the BeagleBone. No changes were made in this
design for the board.

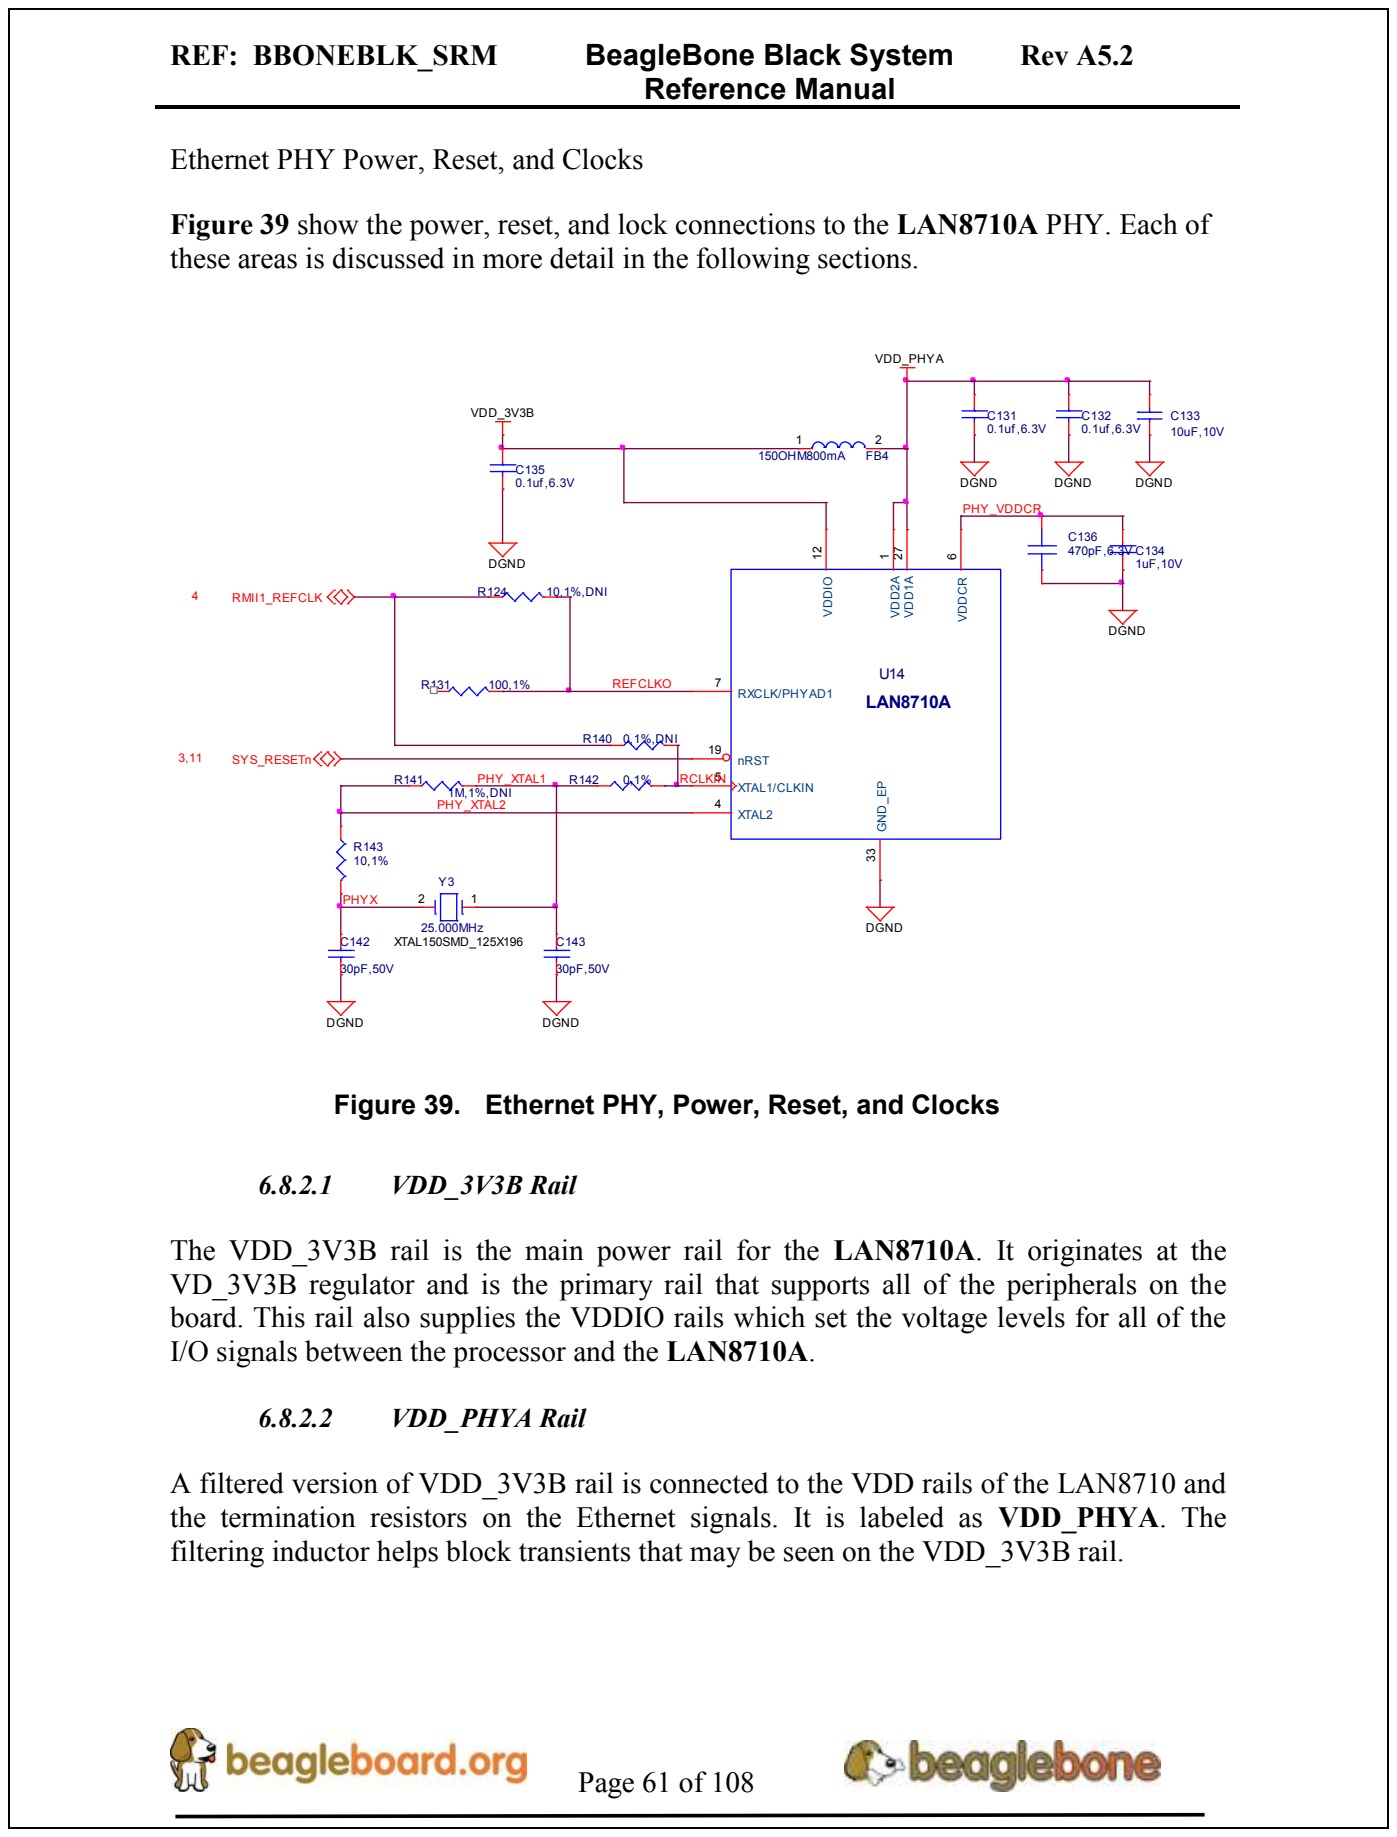
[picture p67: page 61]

Ethernet PHY Power, Reset, and Clocks

Figure 39 show the power, reset, and lock connections to the LAN8710A PHY. Each of
these areas is discussed in more detail in the following sections.

Figure 39. Ethernet PHY, Power, Reset, and Clocks

The VDD_3V3B rail is the main power rail for the LAN8710A. It originates at the
VD_3V3B regulator and is the primary rail that supports all of the peripherals on the
board. This rail also supplies the VDDIO rails which set the voltage levels for all of the
I/O signals between the processor and the LAN8710A.

A filtered version of VDD_3V3B rail is connected to the VDD rails of the LAN8710 and
the termination resistors on the Ethernet signals. It is labeled as VDD_PHYA. The
filtering inductor helps block transients that may be seen on the VDD_3V3B rail.

### 6.8.2.3 PHY_VDDCR Rail

The PHY_VDDCR rail originates inside the LAN8710A. Filter and bypass capacitors are used to filter the rail. Only circuitry inside the LAN8710A uses this rail.

### 6.8.2.4 SYS_RESET

The reset of the LAN8710A is controlled via the SYS_RESETn signal, the main board reset line.

### 6.8.2.5 Clock Signals

A crystal is used to create the clock for the LAN8710A. The processor uses the RMII_RXCLK signal to provide the clocking for the data between the processor and the LAN8710A.

### 6.8.3 LAN8710A Mode Pins

There are mode pins on the LAN8710A that sets the operational mode for the PHY when coming out of reset. These signals are also used to communicate between the processor and the LAN8710A. As a result, these signals can be driven by the processor which can cause the PHY not to be initiated correctly. To insure that this does not happen, three low value pull up resistors are used. Figure 40 below shows the three mode pin resistors.

MODE2

RXD1/MODE1

RXD0/MODE0

R114 1.5K,1%

R112 1.5K,1%

R113 1.5K,1%

VDD_3V3B

Figure 40. Ethernet PHY Mode Pins

This will set the mode to be 111, which enables all modes and enables auto-negotiation.

This design

### 6.9 HDMI Interface

The BeagleBone Black has an onboard HDMI framer that converts the LCD signals and audio signals to drive a HDMI monitor. The design uses an NXP TDA199988 HDMI Framer.

The following sections provide more detail into the design of this interface.

### 6.9.1 Supported Resolutions

The maximum resolution supported by the BeagleBone Black is 1280x1024 @ 60Hz. Table 8 below shows the supported resolutions. Not all resolutions may work on all monitors, but these have been tested and shown to work on at least one monitor. EDID is supported on the BeagleBone Black. Based on the EDID reading from the connected monitor, the highest compatible resolution is selected.

Table 8. | HDMI Supported Monitor Resolutions
800 x 600 @60Hz | 1024 x 768 @75Hz | 1280 x 720 @60
800 x 600 @56Hz | 1024 x 768 @70Hz
640 x 480 @75Hz | 1024 x 768 @60Hz
640 x 480 @60Hz | 800 x 600 @75Hz
720 x 400 @70Hz | 800 x 600 @72Hz
1280 x 1024 @75Hz | 720 x 480 @60Hz

### 6.9.2 HDMI Framer

The TDA19988 is a High-Definition Multimedia Interface (HDMI) 1.4a transmitter. It is backward compatible with DVI 1.0 and can be connected to any DVI 1.0 or HDMI sink. The HDCP mode is not used in the design. The non-HDCP version of the device is used in the BeagleBone Black design.

This device provides additional embedded features like CEC (Consumer Electronic Control). CEC is a single bidirectional bus that transmits CEC over the home appliance network connected through this bus. This eliminates the need of any additional device to handle this feature. While this feature is supported in this device, as of this point, the SW to support this feature has not been implemented and is not a feature that is considered critical.

It can be switched to very low power Standby or Sleep modes to save power when HDMI is not used. TDA19988 embeds I2C-bus master interface for DDC-bus communication to read EDID. This device can be controlled or configured via I2C-bus interface.

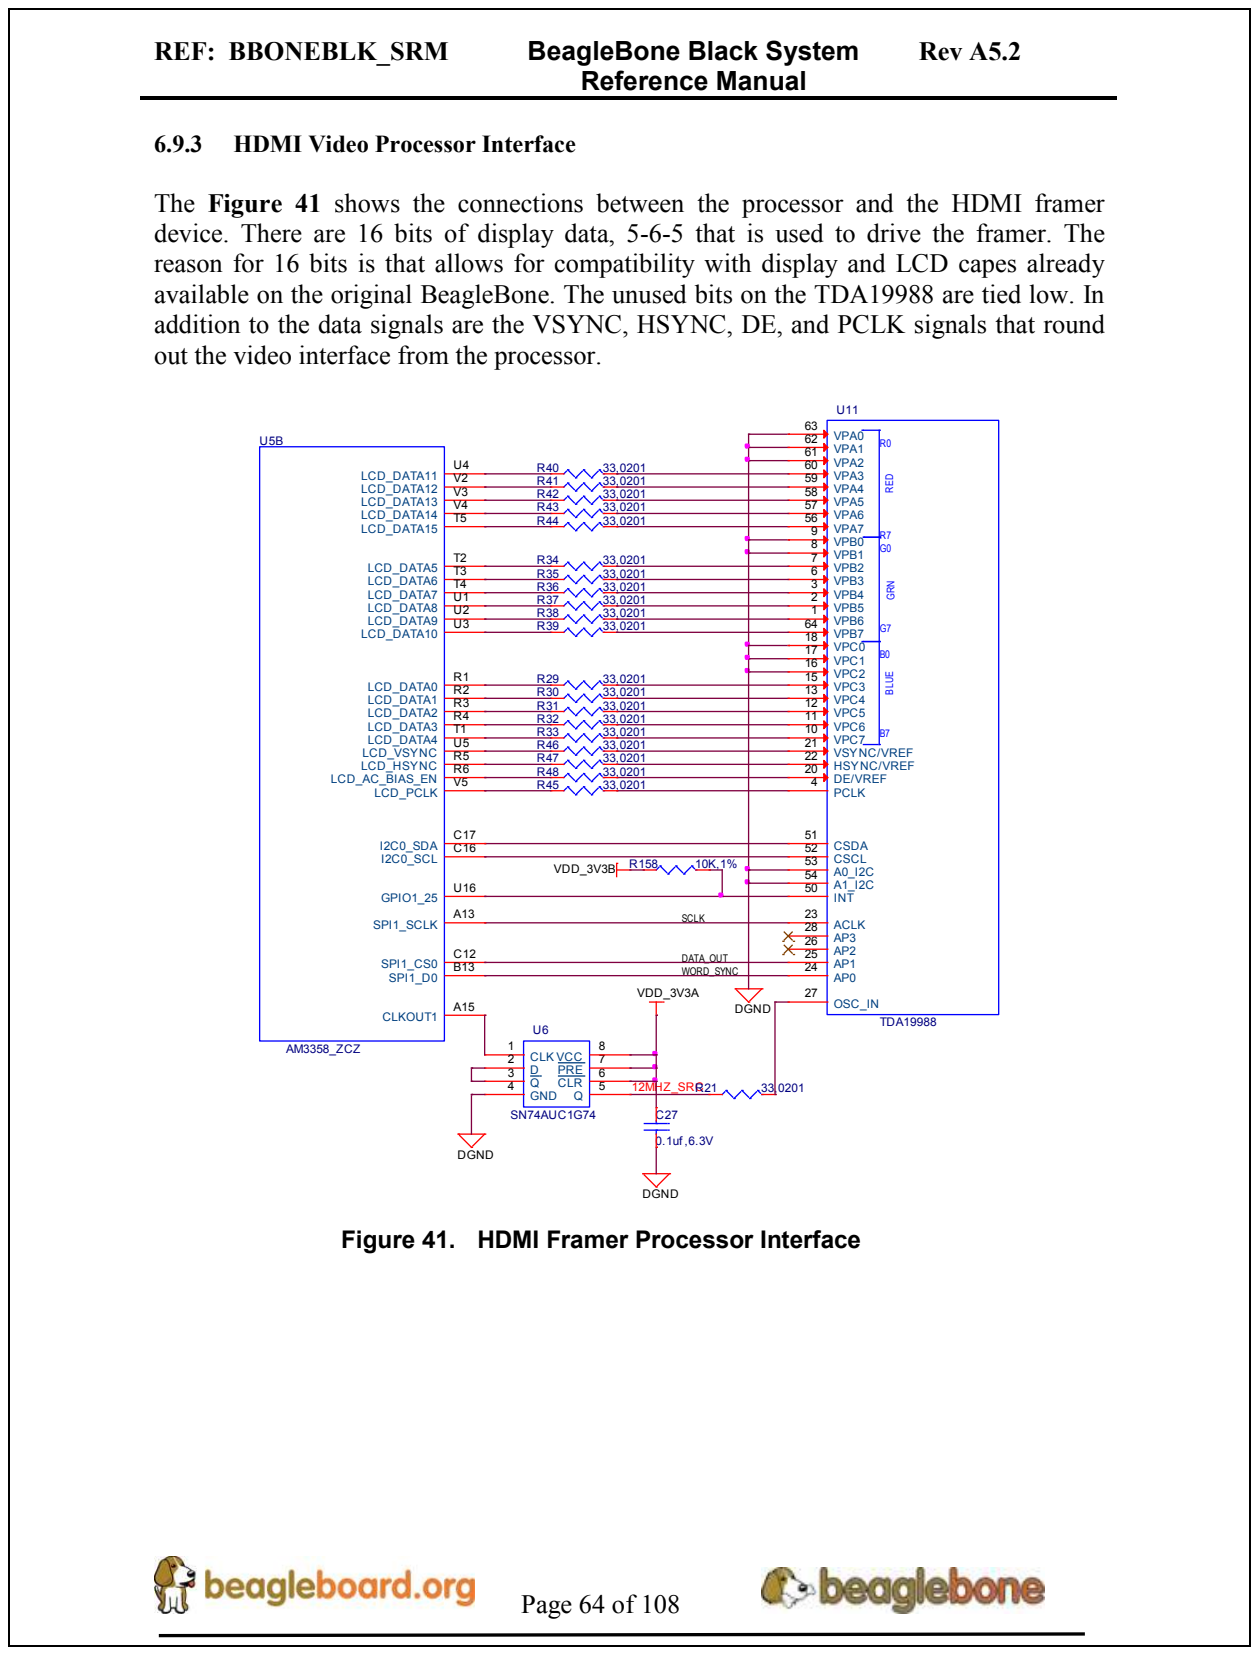
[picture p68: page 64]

6.9.3 HDMI Video Processor Interface

The Figure 41 shows the connections between the processor and the HDMI framer
device. There are 16 bits of display data, 5-6-5 that is used to drive the framer. The
reason for 16 bits is that allows for compatibility with display and LCD capes already
available on the original BeagleBone. The unused bits on the TDA19988 are tied low. In
addition to the data signals are the VSYNC, HSYNC, DE, and PCLK signals that round
out the video interface from the processor.

Figure 41. HDMI Framer Processor Interface

### 6.9.4 HDMI Control Processor Interface

In order to use the TDA19988, the processor needs to setup the device. This is done via the I2C interface between the processor and the TDA19988. There are two signals on the TDA19988 that could be used to set the address of the TDA19988. In this design they are both tied low. The I2C interface supports both 400kHz and 100KhZ operation. Table 9 shows the I2C address.

Table 9. TDA19988 I2C Address

### 6.9.5 Interrupt Signal

There is a HDMI_INT signal that connects from the TDA19988 to the processor. This signal can be used to alert the processor in a state change on the HDMI interface.

### 6.9.6 Audio Interface

There is an I2S audio interface between the processor and the TDA19988. Stereo audio can be transported over the HDMI interface to an audio equipped display. In order to create the required clock frequencies, and external 24.576MHz oscillator, Y4, is used. From this clock, the processor generates the required clock frequencies for the TDA19988.

There are three signals used to pass data from the processor to the TDA19988. SCLK is the serial clock. SPI1_CS0 is the data pin to the TDA19888. SPI1_D0 is the word sync pin. These signals are configured as I2S interfaces.

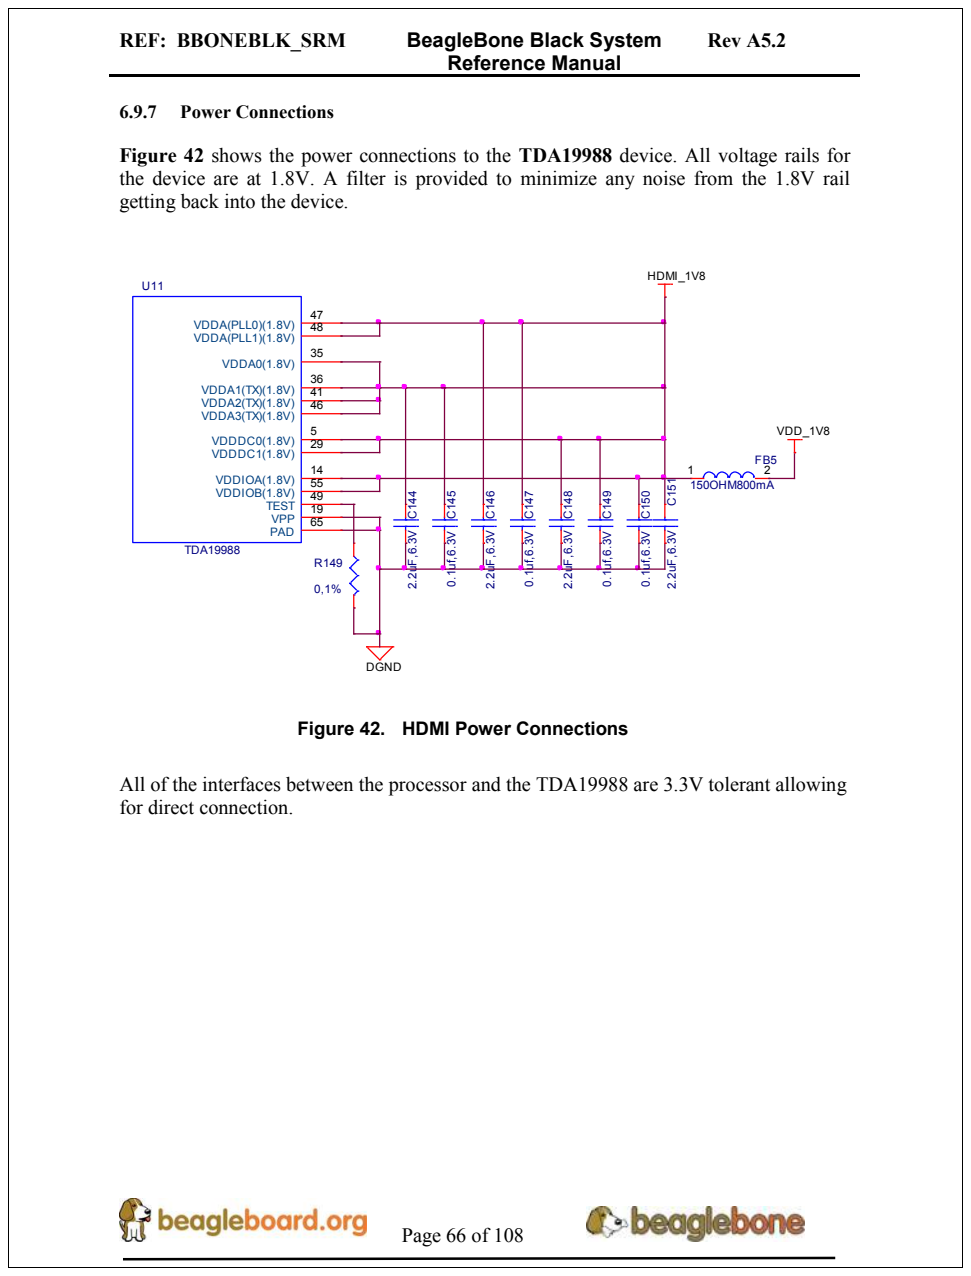
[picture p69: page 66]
6.9.7 Power Connections; 150OHM800mA; HDMI_1V8; DGND; TDA19988; VDDIOA(1.8V); VPP; TEST; VDDA(PLL0)(1.8V); VDDA0(1.8V); VDDA1(TX)(1.8V); VDDDC0(1.8V); VDDDC1(1.8V); VDDA2(TX)(1.8V); VDDA3(TX)(1.8V); VDDA(PLL1)(1.8V); VDDIOB(1.8V); PAD; C¹⁴⁹ 0.1uf,6.3V C¹⁴⁵ 0.1uf,6.3V; C¹⁵⁰ 0.1uf,6.3V C¹⁴⁷ 0.1uf,6.3V; C¹⁵¹ 2.2uF,6.3V

Figure 42 shows the power connections to the TDA19988 device. All voltage rails for
the device are at 1.8V. A filter is provided to minimize any noise from the 1.8V rail
getting back into the device.

VDD_1V8 C¹⁴⁸ 2.2uF,6.3V C¹⁴⁶ 2.2uF,6.3V C¹⁴⁴ 2.2uF,6.3V

Figure 42. HDMI Power Connections

All of the interfaces between the processor and the TDA19988 are 3.3V tolerant allowing
for direct connection.

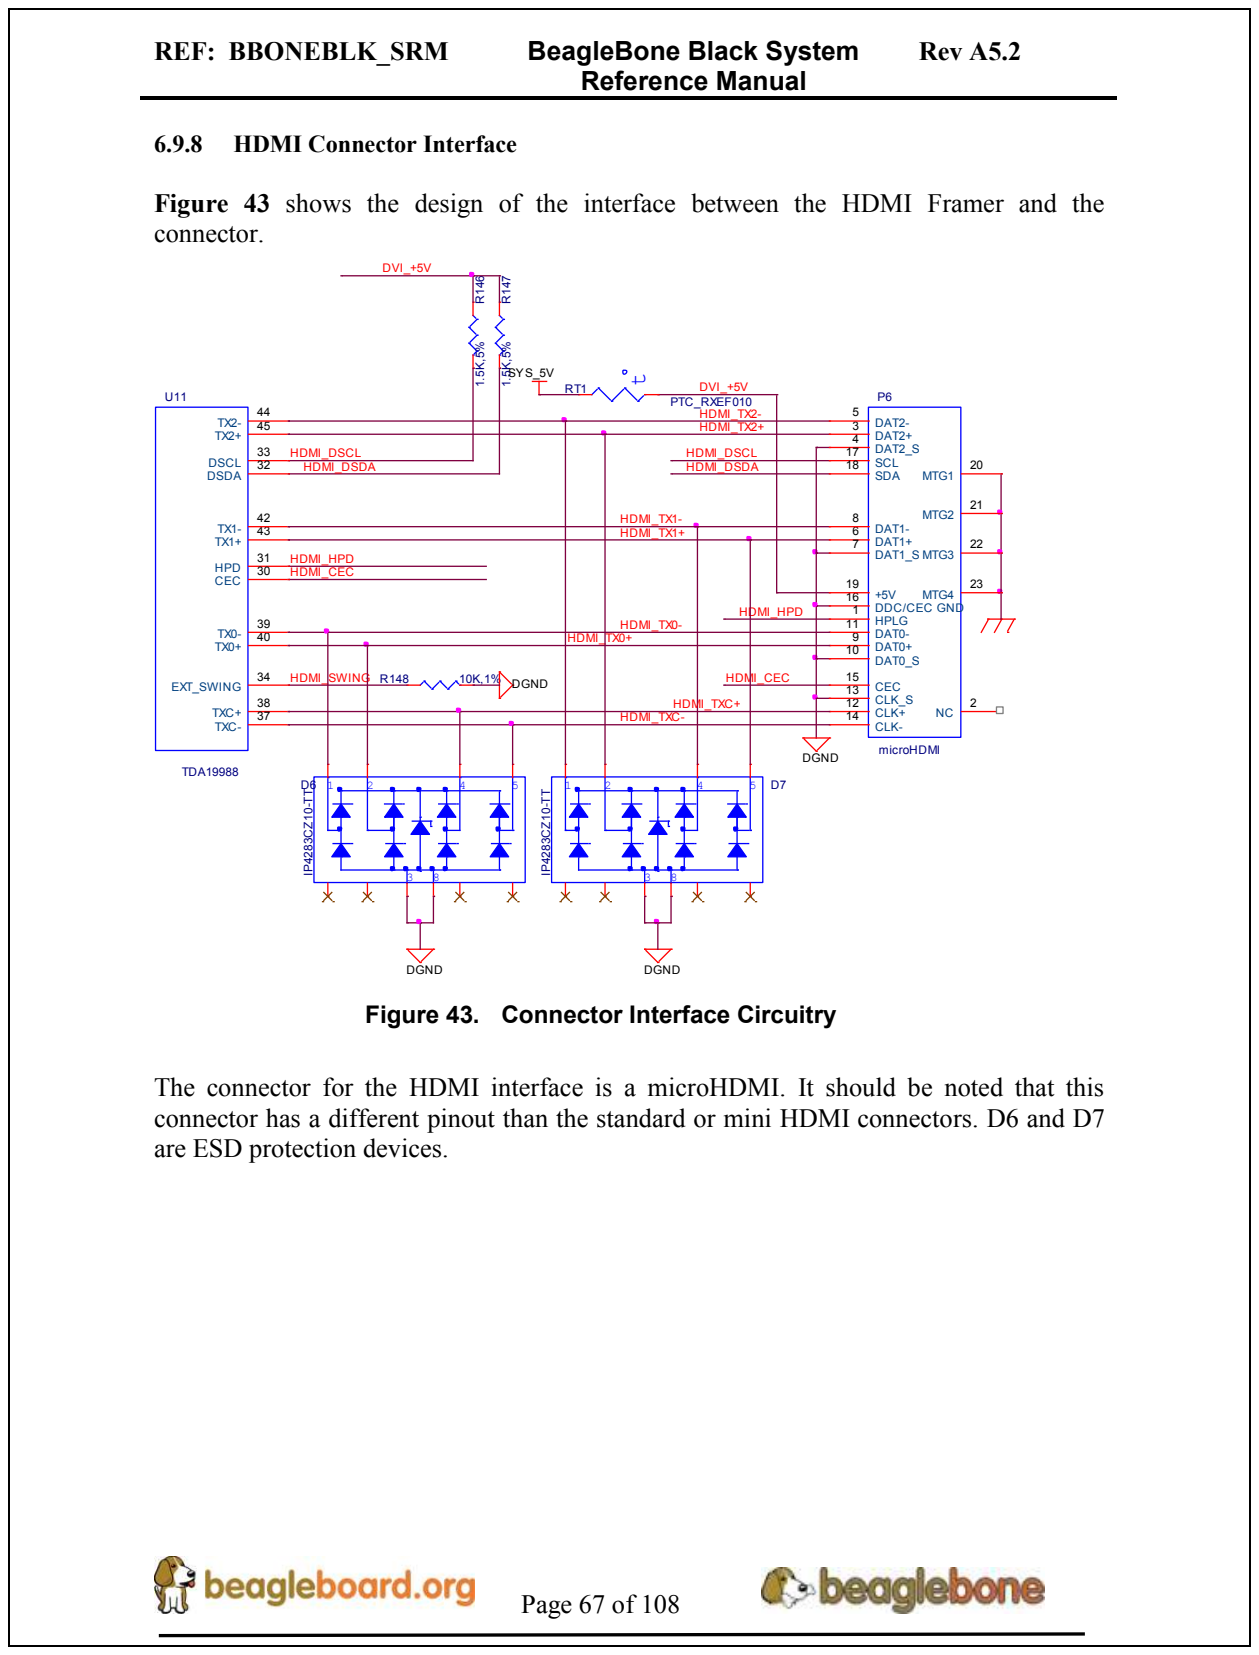
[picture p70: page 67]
HDMI_TX2+; HDMI_TX2-; HDMI_CEC; HDMI_HPD; HDMI_DSDA; HDMI_DSCL R¹⁴⁶ 1.5K,5%; DVI_+5V R¹⁴⁷ 1.5K,5%; DVI_+5V; HDMI_DSCL; DGND HDMI_SWING; TDA19988; DSCL; DSDA; HPD; CEC; TXC+; TXC-; EXT_SWING; D7 IP⁴²⁸³CZ10⁻TT; 5 IP⁴²⁸³CZ10⁻TT; microHDMI; DAT2+; DAT2-; DAT2_S; DAT1+; DAT1_S; DAT1-; DAT0+; DAT0_S; DAT0-; CLK+; CLK-; CLK_S; SCL; SDA; DDC/CEC GND; HPLG; MTG1; MTG2; MTG3; MTG4; PTC_RXEF010; SYS_5V; DGND; HDMI_TX0+; HDMI_TX1-; HDMI_TXC-; HDMI_TXC+; HDMI_TX0-; HDMI_TX1+

6.9.8 HDMI Connector Interface

Figure 43 shows the design of the interface between the HDMI Framer and the
connector.

Figure 43. Connector Interface Circuitry

The connector for the HDMI interface is a microHDMI. It should be noted that this
connector has a different pinout than the standard or mini HDMI connectors. D6 and D7
are ESD protection devices.

### 7.0 Connectors

This section describes each of the connectors on the board.

### 7.1 Expansion Connectors

The expansion interface on the board is comprised of two 46 pin connectors. All signals on the expansion headers are 3.3V unless otherwise indicated.

NOTE: Do not connect 5V logic level signals to these pins or the board will be damaged.

Figure 44 shows the location of the expansion connectors.

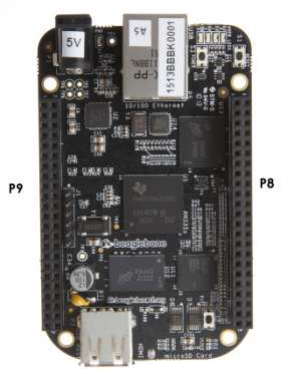
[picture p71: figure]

Figure 44. Expansion Connector Location

The location and spacing of the expansion headers are the same as on the original BeagleBone.

### 7.1.1 Connector P8

Table 10 shows the pinout of the P8 expansion header. Other signals can be connected to this connector based on setting the pin mux on the processor, but this is the default settings on power up. The SW is responsible for setting the default function of each pin. There are some signals that have not been listed here. Refer to the processor documentation for more information on these pins and detailed descriptions of all of the pins listed. In some cases there may not be enough signals to complete a group of signals that may be required to implement a total interface.

The PROC column is the pin number on the processor.
The PIN column is the pin number on the expansion header.
The MODE columns are the mode setting for each pin. Setting each mode to align with the mode column will give that function on that pin.

Reference Manual

Table 10. Expansion Header P8 Pinout

PIN | PROC | NAME | MODE0 | MODE1 | MODE2 | MODE3 | MODE4 | MODE5 | MODE6 | MODE7
1,2 | GND
3 | R9 | GPIO1_6 | gpmc_ad6 | mmc1_dat6 | | | | | | gpio1[6]
4 | T9 | GPIO1_7 | gpmc_ad7 | mmc1_dat7 | | | | | | gpio1[7]
5 | R8 | GPIO1_2 | gpmc_ad2 | mmc1_dat2 | | | | | | gpio1[2]
6 | T8 | GPIO1_3 | gpmc_ad3 | mmc1_dat3 | | | | | | gpio1[3]
7 | R7 | TIMER4 | gpmc_advn_ale | | timer4 | | | | | gpio2[2]
8 | T7 | TIMER7 | gpmc_oen_ren | | timer7 | | | | | gpio2[3]
9 | T6 | TIMER5 | gpmc_be0n_cle | | timer5 | | | | | gpio2[5]
10 | U6 | TIMER6 | gpmc_wen | | timer6 | | | | | gpio2[4]
11 | R12 | GPIO1_13 | gpmc_ad13 | lcd_data18 | mmc1_dat5 | mmc2_dat1 | eQEP2B_in | | | gpio1[13]
12 | T12 | GPIO1_12 | GPMC_AD12 | LCD_DATA19 | Mmc1_dat4 | MMC2_DAT0 | EQEP2A_IN | | | gpio1[12]
13 | T10 | EHRPWM2B | gpmc_ad9 | lcd_data22 | mmc1_dat1 | mmc2_dat5 | ehrpwm2B | | | gpio0[23]
14 | T11 | GPIO0_26 | gpmc_ad10 | lcd_data21 | mmc1_dat2 | mmc2_dat6 | ehrpwm2_tripzone_in | | | gpio0[26]
15 | U13 | GPIO1_15 | gpmc_ad15 | lcd_data16 | mmc1_dat7 | mmc2_dat3 | eQEP2_strobe | | | gpio1[15]
16 | V13 | GPIO1_14 | gpmc_ad14 | lcd_data17 | mmc1_dat6 | mmc2_dat2 | eQEP2_index | | | gpio1[14]
17 | U12 | GPIO0_27 | gpmc_ad11 | lcd_data20 | mmc1_dat3 | mmc2_dat7 | ehrpwm0_synco | | | gpio0[27]
18 | V12 | GPIO2_1 | gpmc_clk_mux0 | lcd_memory_clk | gpmc_wait1 | mmc2_clk | | | mcasp0_fsr | gpio2[1]
19 | U10 | EHRPWM2A | gpmc_ad8 | lcd_data23 | mmc1_dat0 | mmc2_dat4 | ehrpwm2A | | | gpio0[22]
20 | V9 | GPIO1_31 | gpmc_csn2 | gpmc_be1n | mmc1_cmd | | | | | gpio1[31]
21 | U9 | GPIO1_30 | gpmc_csn1 | gpmc_clk | mmc1_clk | | | | | gpio1[30]
22 | V8 | GPIO1_5 | gpmc_ad5 | mmc1_dat5 | | | | | | gpio1[5]
23 | U8 | GPIO1_4 | gpmc_ad4 | mmc1_dat4 | | | | | | gpio1[4]
24 | V7 | GPIO1_1 | gpmc_ad1 | mmc1_dat1 | | | | | | gpio1[1]
25 | U7 | GPIO1_0 | gpmc_ad0 | mmc1_dat0 | | | | | | gpio1[0]
26 | V6 | GPIO1_29 | gpmc_csn0 | | | | | | | gpio1[29]
27 | U5 | GPIO2_22 | lcd_vsync | gpmc_a8 | | | | | | gpio2[22]
28 | V5 | GPIO2_24 | lcd_pclk | gpmc_a10 | | | | | | gpio2[24]
29 | R5 | GPIO2_23 | lcd_hsync | gpmc_a9 | | | | | | gpio2[23]
30 | R6 | GPIO2_25 | lcd_ac_bias_en | gpmc_a11 | | | | | | gpio2[25]
31 | V4 | UART5_CTSN | lcd_data14 | gpmc_a18 | eQEP1_index | mcasp0_axr1 | uart5_rxd | | uart5_ctsn | gpio0[10]
32 | T5 | UART5_RTSN | lcd_data15 | gpmc_a19 | eQEP1_strobe | mcasp0_ahclkx | mcasp0_axr3 | | uart5_rtsn | gpio0[11]
33 | V3 | UART4_RTSN | lcd_data13 | gpmc_a17 | eQEP1B_in | mcasp0_fsr | mcasp0_axr3 | | uart4_rtsn | gpio0[9]
34 | U4 | UART3_RTSN | lcd_data11 | gpmc_a15 | ehrpwm1B | mcasp0_ahclkr | mcasp0_axr2 | | uart3_rtsn | gpio2[17]
35 | V2 | UART4_CTSN | lcd_data12 | gpmc_a16 | eQEP1A_in | mcasp0_aclkr | mcasp0_axr2 | | uart4_ctsn | gpio0[8]
36 | U3 | UART3_CTSN | lcd_data10 | gpmc_a14 | ehrpwm1A | mcasp0_axr0 | | | uart3_ctsn | gpio2[16]
37 | U1 | UART5_TXD | lcd_data8 | gpmc_a12 | ehrpwm1_tripzone_in | mcasp0_aclkx | uart5_txd | | uart2_ctsn | gpio2[14]
38 | U2 | UART5_RXD | lcd_data9 | gpmc_a13 | ehrpwm0_synco | mcasp0_fsx | uart5_rxd | | uart2_rtsn | gpio2[15]
39 | T3 | GPIO2_12 | lcd_data6 | gpmc_a6 | | eQEP2_index | | | | gpio2[12]
40 | T4 | GPIO2_13 | lcd_data7 | gpmc_a7 | | eQEP2_strobe | pr1_edio_data_out7 | | | gpio2[13]
41 | T1 | GPIO2_10 | lcd_data4 | gpmc_a4 | | eQEP2A_in | | | | gpio2[10]
42 | T2 | GPIO2_11 | lcd_data5 | gpmc_a5 | | eQEP2B_in | | | | gpio2[11]
43 | R3 | GPIO2_8 | lcd_data2 | gpmc_a2 | | ehrpwm2_tripzone_in | | | | gpio2[8]
44 | R4 | GPIO2_9 | lcd_data3 | gpmc_a3 | | ehrpwm0_synco | | | | gpio2[9]
45 | R1 | GPIO2_6 | lcd_data0 | gpmc_a0 | | ehrpwm2A | | | | gpio2[6]
46 | R2 | GPIO2_7 | lcd_data1 | gpmc_a1 | | ehrpwm2B | | | | gpio2[7]

### 7.1.2 Connector P9

Table 11 lists the signals on connector P9. Other signals can be connected to this connector based on setting the pin mux on the processor, but this is the default settings on power up.

There are some signals that have not been listed here. Refer to the processor documentation for more information on these pins and detailed descriptions of all of the pins listed. In some cases there may not be enough signals to complete a group of signals that may be required to implement a total interface.

The PROC column is the pin number on the processor.
The PIN column is the pin number on the expansion header.
The MODE columns are the mode setting for each pin. Setting each mode to align with the mode column will give that function on that pin.

NOTES:

In the table are the following notations:

PWR_BUT is a 5V level as pulled up internally by the TPS65217C. It is activated by pulling the signal to GND.

# Both of these signals connect to pin 41 of P11. Resistors are installed that allow for the GPIO3_20 connection to be removed by removing R221. The intent is to allow the SW to use either of these signals, one or the other, on pin 41. SW should set the unused pin in input mode when using the other pin. This allowed us to get an extra signal out to the expansion header.

@ Both of these signals connect to pin 42 of P11. Resistors are installed that allow for the GPIO3_18 connection to be removed by removing R202. The intent is to allow the SW to use either of these signals, on pin 42. SW should set the unused pin in input mode when using the other pin. This allowed us to get an extra signal out to the expansion header.

Reference Manual

Table 11. Expansion Header P9 Pinout

PIN | PROC | NAME | MODE0 | MODE1 | MODE2 | MODE3 | MODE4 | MODE5 | MODE6 | MODE7
1,2 | GND
3,4 | DC_3.3V
5,6 | VDD_5V
7,8 | SYS_5V
9 | PWR_BUT
10 | A10 | SYS_RESETn | RESET_OUT
11 | T17 | UART4_RXD | gpmc_wait0 | mii2_crs | gpmc_csn4 | rmii2_crs_dv | mmc1_sdcd | | uart4_rxd_mux2 | gpio0[30]
12 | U18 | GPIO1_28 | gpmc_be1n | mii2_col | gpmc_csn6 | mmc2_dat3 | gpmc_dir | | mcasp0_aclkr_mux3 | gpio1[28]
13 | U17 | UART4_TXD | gpmc_wpn | mii2_rxerr | gpmc_csn5 | rmii2_rxerr | mmc2_sdcd | | uart4_txd_mux2 | gpio0[31]
14 | U14 | EHRPWM1A | gpmc_a2 | mii2_txd3 | rgmii2_td3 | mmc2_dat1 | gpmc_a18 | | ehrpwm1A_mux1 | gpio1[18]
15 | R13 | GPIO1_16 | gpmc_a0 | gmii2_txen | rmii2_tctl | mii2_txen | gpmc_a16 | | ehrpwm1_tripzone_input | gpio1[16]
16 | T14 | EHRPWM1B | gpmc_a3 | mii2_txd2 | rgmii2_td2 | mmc2_dat2 | gpmc_a19 | | ehrpwm1B_mux1 | gpio1[19]
17 | A16 | I2C1_SCL | spi0_cs0 | mmc2_sdwp | I2C1_SCL | ehrpwm0_synci | | | | gpio0[5]
18 | B16 | I2C1_SDA | spi0_d1 | mmc1_sdwp | I2C1_SDA | ehrpwm0_tripzone | | | | gpio0[4]
19 | D17 | I2C2_SCL | uart1_rtsn | timer5 | dcan0_rx | I2C2_SCL | spi1_cs1 | | | gpio0[13]
20 | D18 | I2C2_SDA | uart1_ctsn | timer6 | dcan0_tx | I2C2_SDA | spi1_cs0 | | | gpio0[12]
21 | B17 | UART2_TXD | spi0_d0 | uart2_txd | I2C2_SCL | ehrpwm0B | | | EMU3_mux1 | gpio0[3]
22 | A17 | UART2_RXD | spi0_sclk | uart2_rxd | I2C2_SDA | ehrpwm0A | | | EMU2_mux1 | gpio0[2]
23 | V14 | GPIO1_17 | gpmc_a1 | gmii2_rxdv | rgmii2_rxdv | mmc2_dat0 | gpmc_a17 | | ehrpwm0_synco | gpio1[17]
24 | D15 | UART1_TXD | uart1_txd | mmc2_sdwp | dcan1_rx | I2C1_SCL | | | | gpio0[15]
25 | A14 | GPIO3_21 | mcasp0_ahclkx | eQEP0_strobe | mcasp0_axr3 | mcasp1_axr1 | EMU4_mux2 | | | gpio3[21]
26 | D16 | UART1_RXD | uart1_rxd | mmc1_sdwp | dcan1_tx | I2C1_SDA | | | | gpio0[14]
27 | C13 | GPIO3_19 | mcasp0_fsr | eQEP0B_in | mcasp0_axr3 | mcasp1_fsx | EMU2_mux2 | | | gpio3[19]
28 | C12 | SPI1_CS0 | mcasp0_ahclkr | ehrpwm0_synci | mcasp0_axr2 | spi1_cs0 | eCAP2_in_PWM2_out | | | gpio3[17]
29 | B13 | SPI1_D0 | mcasp0_fsx | ehrpwm0B | | spi1_d0 | mmc1_sdcd_mux1 | | | gpio3[15]
30 | D12 | SPI1_D1 | mcasp0_axr0 | ehrpwm0_tripzone | | spi1_d1 | mmc2_sdcd_mux1 | | | gpio3[16]
31 | A13 | SPI1_SCLK | mcasp0_aclkx | ehrpwm0A | | spi1_sclk | mmc0_sdcd_mux1 | | | gpio3[14]
32 | VADC
33 | C8 | AIN4
34 | AGND
35 | A8 | AIN6
36 | B8 | AIN5
37 | B7 | AIN2
38 | A7 | AIN3
39 | B6 | AIN0
40 | C7 | AIN1
41# | D14 | CLKOUT2 | xdma_event_intr1 | | tclkin | clkout2 | timer7_mux1 | | EMU3_mux0 | gpio0[20]
D13 | GPIO3_20 | mcasp0_axr1 | eQEP0_index | | Mcasp1_axr0 | emu3 | | | gpio3[20]
42@ | C18 | GPIO0_7 | eCAP0_in_PWM0_out | uart3_txd | spi1_cs1 | pr1_ecap0_ecap_capin_apwm_o | spi1_sclk | mmc0_sdwp | xdma_event_intr2 | gpio0[7]
B12 | GPIO3_18 | Mcasp0_aclkr | eQEP0A_in | Mcaspo_axr2 | Mcasp1_aclkx | gpio3[18]
43-46 | GND
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

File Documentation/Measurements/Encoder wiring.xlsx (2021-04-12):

CP32 - Connected to DSpace | Pin | Connected to | Color
VCC (+5 V) | 1 | 2 | Red
PHI0 | 2 | 5 | Green
PHI0- | 3 | 6 | Blue
Phi90 | 4 | 7 | Purple
PHI90- | 5 | 8 | Grey
INDEX | 6 | 10 | White
INDEX- | 7 | 9 | Black
GND | 8 | 3 | Orange
Not Connected | 9
Not Connected | 10
Not Connected | 11
Not Connected | 12
Not Connected | 13
Not Connected | 14
Not Connected | 15
Encoder cable | Pin | Connected to
Not Connected | 1 |  | Brown
V supply | 2 | 1 | Red
GND | 3 | 8 | Orange
Not Connected | 4 |  | Yellow
A Quadrature 1 | 5 | 2 | Green
A- | 6 | 3 | Blue
B Quadrature 2 | 7 | 4 | Purple
B- | 8 | 5 | Gray
Z- | 9 | 7 | White
Z Index | 10 | 6 | Black

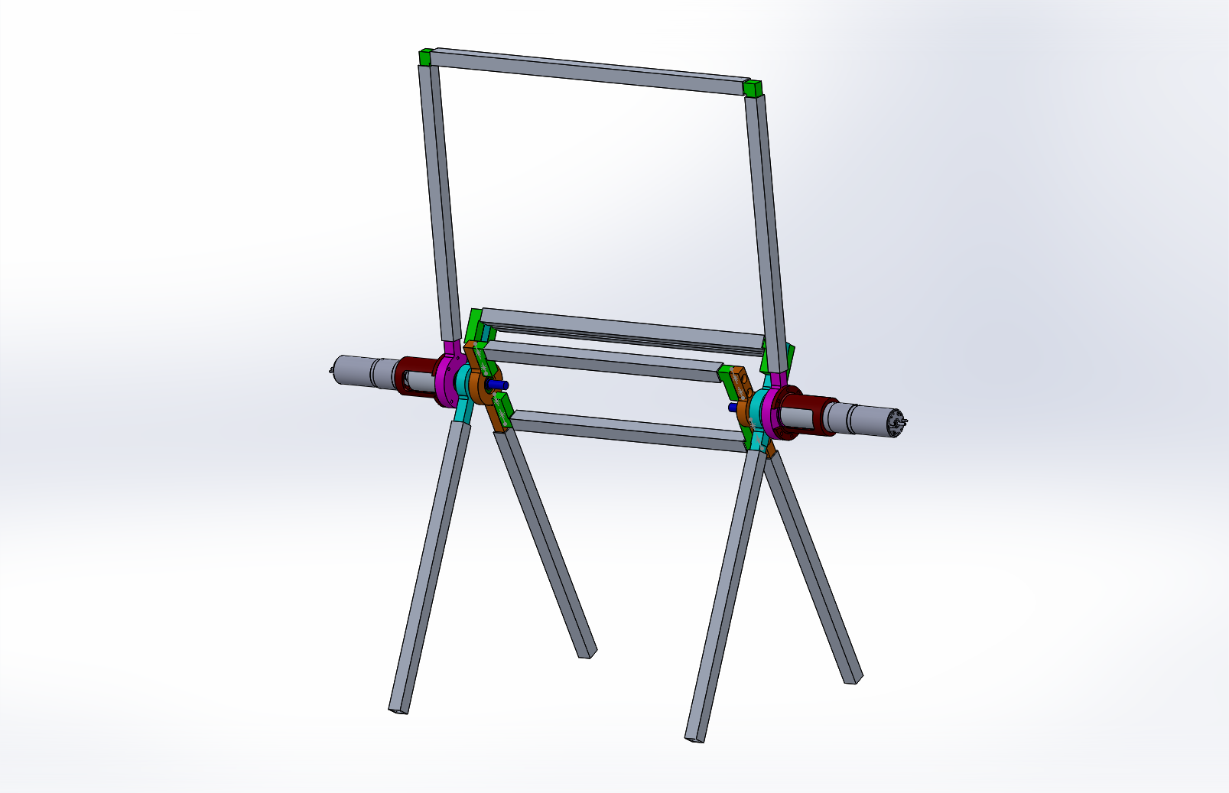
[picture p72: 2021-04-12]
Documentation/CAD/Design_HIP16mm/Main_Assembly_002.PNG

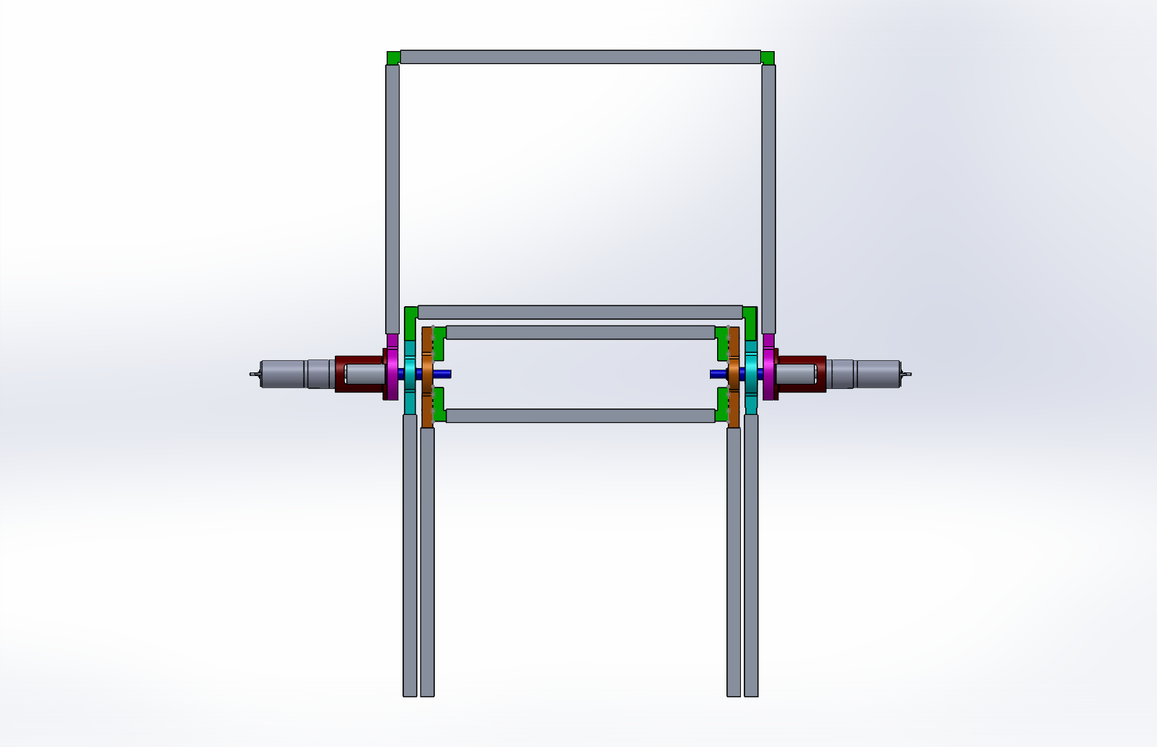
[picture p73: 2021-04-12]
Documentation/CAD/Design_HIP16mm/Main_Assembly_001.PNG

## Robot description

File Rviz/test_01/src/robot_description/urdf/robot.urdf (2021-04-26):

<?xml version="1.0"?>
<robot name="origins">
  <link name="base_link">
    <visual>
      <material name="gray">
        <color rgba="0.4 0.4 0.4 2"/>
      </material>
      <origin rpy="1.57075 0 0" xyz="0 0 0.7"/>
    </visual>
  </link>  
  
  <link name="torso">
    <visual>
      <geometry>
        <mesh filename="package://robot_description/STL/body_link.stl" scale="0.001 0.001 0.001"/>
      </geometry>
      <material name="gray">
        <color rgba="0.4 0.4 0.4 2"/>
      </material>
      <origin rpy="1.57075 0 0" xyz="0 0 0.7"/>
    </visual>
  </link>

  <link name="leg_01">
    <visual>
      <geometry>
        <mesh filename="package://robot_description/STL/leg_01.stl" scale="0.001 0.001 0.001"/>
      </geometry>
      <material name="gray">
        <color rgba="0.4 0.4 0.4 0.2"/>
      </material>
      <origin rpy="1.57075 0 0" xyz="0 0 0"/>
    </visual>
  </link>  
  
  <link name="leg_02">
    <visual>
      <geometry>
        <mesh filename="package://robot_description/STL/leg_02.stl" scale="0.001 0.001 0.001"/>
      </geometry>
      <material name="gray">
        <color rgba="0.4 0.4 0.4 1.0"/>
      </material>
      <origin rpy="1.57075 0 0" xyz="0 0 0"/>
    </visual>
  </link>

  <joint name="base_to_leg_01" type="revolute">
    <parent link="base_link"/>
    <child link="leg_01"/>
    <origin xyz="0 0 0.7"/>
    <limit lower="-1.5708" upper="1.5708" effort="10" velocity="3"/>
  </joint>

  <joint name="base_to_leg_02" type="revolute">
    <parent link="base_link"/>
    <child link="leg_02"/>
    <origin xyz="0 0 0.7"/>
    <limit lower="-1.5708" upper="1.5708" effort="10" velocity="3"/>
  </joint>

  <joint name="base_to_torso" type="revolute">
    <parent link="base_link"/>
    <child link="torso"/>
    <origin xyz="0 0 0"/>
    <limit lower="-1.5708" upper="1.5708" effort="10" velocity="3"/>
  </joint>
</robot>

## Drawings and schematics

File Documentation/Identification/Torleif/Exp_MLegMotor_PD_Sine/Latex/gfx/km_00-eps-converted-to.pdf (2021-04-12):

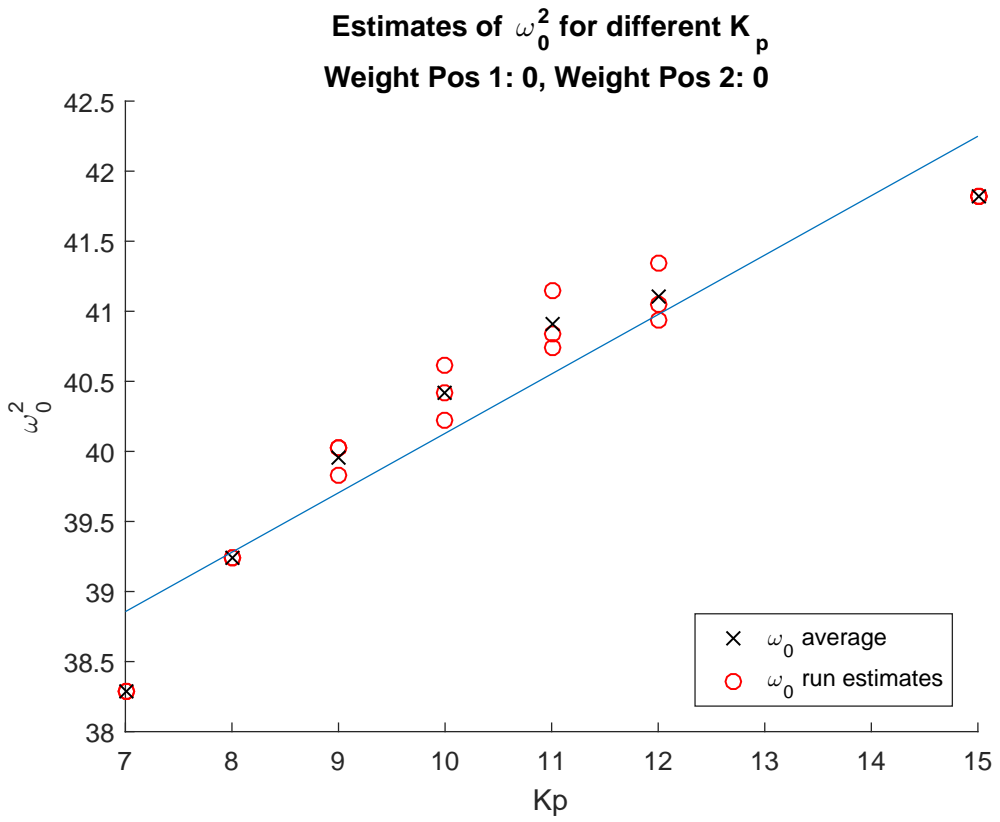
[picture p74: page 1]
for different K; average; run estimates

Estimates of ω
Weight Pos 1: 0, Weight Pos 2: 0

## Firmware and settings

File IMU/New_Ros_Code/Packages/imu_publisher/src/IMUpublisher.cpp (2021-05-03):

#include "ros/ros.h"
#include "std_msgs/Float32MultiArray.h"
#include "std_msgs/String.h"
#include "messages_pkg/IMU_settings.h"
#include "messages_pkg/imu_angles.h"

#include <iostream>
#include <sstream>
#include <unistd.h>
#include <cmath>
#include <linux/i2c-dev.h>
#include <linux/i2c.h>
#include <sys/ioctl.h>
#include <fcntl.h>
#include <math.h>

#define g_sens_accs 0.061 //value from datasheet page 12
#define PI 3.14159 // constant pi
#define LPS 60 // Loops per second




class LSM9DS1
{
    private :

    int file;
    char addr;
    float ax, ay, az, gx, gy, gz;
    short s_ax, s_ay, s_az, s_gx, s_gy, s_gz;
    float pitch,roll;

    float gyroDrift;

    char dataBuffer[5] = {0};
    char dataBuffer2[5] = {0};

    void convertAccelData()
    {
        s_ax = ((dataBuffer2[1] << 8) | dataBuffer2[0]); 
        s_ay = ((dataBuffer2[3] << 8) | dataBuffer2[2]);
        s_az = ((dataBuffer2[5] << 8) | dataBuffer2[4]);
        ax = (s_ax*g_sens_accs)/1000;
        ay = (s_ay*g_sens_accs)/1000;
        az = (s_az*g_sens_accs)/1000;
        
        roll = atan2(ay,ax);

        roll  *= 180.0 / PI;
    }

    void convertGyroData()
    {
        s_gx = ((dataBuffer[1] << 8) | dataBuffer[0]); 
        s_gy = ((dataBuffer[3] << 8) | dataBuffer[2]);
        s_gz = ((dataBuffer[5] << 8) | dataBuffer[4]);
        gx = (s_gx * 0.0175);
        gy = (s_gy * 0.0175);
        gz = (s_gz * 0.0175);
    }

    public :
    LSM9DS1(char address)
    {
        addr = address;
    }

    void setRegSensor(char reg,char value)
    {
        char *bus ="/dev/i2c-2";
        //Open I2C bus, checks connection
        if((file = open(bus, O_RDWR)) < 0)
        {
            printf("Failed to open bus. \n");
            exit(1);
        }
        ioctl(file, I2C_SLAVE, addr);

        char config[2] = {0};
        config[0] = reg;
        config[1] = value;
        if(write(file, config, 2) < 0)
        {
            printf("Failed to open bus. \n");
            exit(1);
        }
        else
        printf("sucessful init \n");

    }

    void ReadSensor()
    {
        char regis[1] = {0x18};
        write(file, regis, 1);
    
        if(read(file, dataBuffer, 6) != 6)
        {
            printf("Input/Output error \n");
            exit(1);
        }
        convertGyroData();


        char regis2[1] = {0x28};
        write(file, regis2, 1);

        if(read(file, dataBuffer2, 6) != 6)
        {
            printf("Input/Output error \n");
            exit(1);
        }

        convertAccelData();

    }

    void closeSensor()
    {
        close(file);
    }

    void setGyroDrift(float drift)
    {
        gyroDrift = drift;
    }

    float GetGyroDrift(){return gyroDrift;}
    float GetAccelerationX(){ return ax;}
    float GetAccelerationY(){ return ay;}
    float GetAccelerationZ(){ return az;}
    float GetGRotationX(){ return gx;}
    float GetGRotationY(){ return gy;}
    float GetGRotationZ(){ return gz;}
    float GetRotation(){ return roll;}
};

float KP = 0.0;
float KI = 0.0001;


class kalmanFilter
{
    private :
    //end in pre = pre update, post = post update
    //last means it was the value in the previus run
    float XEstimateCurrentPre;
    float XEstimateCurrentPost;
    float XEstimateLastPost = 0.0;
    float UMeasuredLast = 0.0;
    float DeltaT = 1.0/(float)LPS;
    float PCurrentPre;
    float PCurrentPost;
    float PLastPost = 0.0;
    float Q = 0.01;
    float R = 10;
    float YCurrent;
    float KCurrent;

    public :

    kalmanFilter(float q, float r)
    {   
        Q = q;
        R = r;
    }

    void set_QR(float q, float r)
    {   
        Q = q;
        R = r;
    }

    float Filter(float gyro_value, float acceleration_value)
    {
        //prediction
        XEstimateCurrentPre = XEstimateLastPost + UMeasuredLast * DeltaT;
        PCurrentPre = PLastPost + Q;
        //Update
        YCurrent = acceleration_value - XEstimateCurrentPre;
        KCurrent = PCurrentPre/(R + PCurrentPre);
        XEstimateCurrentPost = XEstimateCurrentPre + KCurrent * YCurrent;
        PCurrentPost = (1 - KCurrent) * PCurrentPre;
        //transfer the value to the next cycle
        XEstimateLastPost = XEstimateCurrentPost;
        PLastPost = PCurrentPost;
        UMeasuredLast = gyro_value;

        return(XEstimateCurrentPost);
    }
};


class pi_reg
{
    private :

    float _Kp;
    float _Ki;
    double _integral;
    float pout;
    float iout;
    float error;

    public :

    pi_reg(float Kp, float Ki)
    {
        _Kp = Kp;
        _Ki = Ki;
    }

    void change_PI(float Kp, float Ki)
    {
        _Kp = Kp;
        _Ki = Ki;
    }

    float pi_regulate(float value, float setPoint)
    {
        error = value - setPoint;

        pout = error * _Kp;

        _integral += error * _Ki / LPS;
        iout = _integral;

        return (pout + iout);
    }

    void resetI()
    {
        _integral = 0.0;
    }


    float getError(){ return error;}
};

kalmanFilter KFilter1(0.01, 10);
kalmanFilter KFilter2(0.01, 10);


pi_reg offsetRegulator1(KP, KI);
pi_reg offsetRegulator2(KP, KI);
int Ireset = 0;
float offset1 = 0.0;
float offset2 = 0.0;
float finalAngle1 = 0.0;
float finalAngle2 = 0.0;

void chatterCallback(const messages_pkg::IMU_settings msg)
{
    offsetRegulator1.change_PI(msg.KP, msg.KI);
    offsetRegulator2.change_PI(msg.KP, msg.KI);
    KFilter1.set_QR(msg.KP,msg.KI);
    KFilter1.set_QR(msg.KP,msg.KI);
    if (msg.Ireset != Ireset)
    {
        offsetRegulator1.resetI();
        offsetRegulator2.resetI();
        Ireset = msg.Ireset;
        finalAngle1 = 0;
        finalAngle2 = 0;
    }
}



int main(int argc, char* argv[])
{
    //init
    ros::init(argc, argv, "IMUpublisher");
    //message code
    ros::NodeHandle n;
    ros::Publisher chatter_pub = n.advertise<messages_pkg::imu_angles>("leg_ground_angles", 1);
    ros::Subscriber sub = n.subscribe("IMU_settings",1 ,chatterCallback);
    ros::Rate loop_rate(LPS);
    messages_pkg::imu_angles angles;

    

    //IMU code
    char addresse = 0x6a;
    LSM9DS1 IMU1(addresse);
    addresse = 0x6b;
    LSM9DS1 IMU2(addresse);


    char aksereg = 0x10;
    char setBit  = 0x49;// 3 gyroscope data output rate, 2 fullscale selection, 1=0, 2 gyroscope bandwidth selection
    IMU1.setRegSensor(aksereg,setBit);
    IMU2.setRegSensor(aksereg,setBit);
    aksereg = 0x11;
    setBit  = 0x00;// 4=0, 2 interupt selsction, 2 output selection
    IMU1.setRegSensor(aksereg,setBit);
    IMU2.setRegSensor(aksereg,setBit);
    aksereg = 0x12;
    setBit  = 0x08; // 1 Low power mode enable, 1 high-pass filter enable, 2=0, 4 gyroscope highpass filter bandwidth selsction
    IMU1.setRegSensor(aksereg,setBit);
    IMU2.setRegSensor(aksereg,setBit);
    aksereg = 0x20;
    setBit  = 0x00;// 3 accelerometer output datarate, 2 accelerometer full scale selection, 1 bandwidth rate output datarate, 2 aintialiaasing filter bw rate
    IMU1.setRegSensor(aksereg,setBit);
    IMU2.setRegSensor(aksereg,setBit);
    aksereg = 0x23;
    setBit  = 0x00;//FIFO dissable
    IMU1.setRegSensor(aksereg,setBit);
    IMU2.setRegSensor(aksereg,setBit);
    aksereg = 0x2E;
    setBit  = 0x00;// FIFO dissable
    IMU1.setRegSensor(aksereg,setBit);
    IMU2.setRegSensor(aksereg,setBit);

    float gyro_rotation1 = 0.0;
    float acceleration_rotation1 = 0.0;
    float gyro_rotation2 = 0.0;
    float acceleration_rotation2 = 0.0;
    float total_rotaion = 0.0;

    int calibrationLoopCounter = 0;
    
 


    
    while (calibrationLoopCounter < 1000)
    {
        IMU1.ReadSensor();
        IMU2.ReadSensor();
        gyro_rotation1 += (IMU1.GetGRotationZ());
        gyro_rotation2 += (IMU2.GetGRotationZ());
        calibrationLoopCounter += 1;

    }

    IMU1.setGyroDrift(gyro_rotation1/1000);
    IMU2.setGyroDrift(gyro_rotation2/1000);


    gyro_rotation2 = 0.0;
    gyro_rotation1 = 0.0;


    while (ros::ok())
    {

        IMU1.ReadSensor();
        IMU2.ReadSensor();

        //PID Code
        /*
        acceleration_rotation1 = IMU1.GetRotation();
        gyro_rotation1 += (IMU1.GetGRotationZ()/LPS) - IMU1.GetGyroDrift();
        acceleration_rotation2 = IMU2.GetRotation();
        gyro_rotation2 += (IMU2.GetGRotationZ()/LPS) - IMU2.GetGyroDrift();

        offset1 = offsetRegulator1.pi_regulate(finalAngle1, acceleration_rotation1);
        offset2 = offsetRegulator2.pi_regulate(finalAngle2, acceleration_rotation2);

        //ROS_INFO("%f ", accelerationAngleList[LPS]);
        finalAngle1 = gyro_rotation1 - offset1;
        finalAngle2 = gyro_rotation2 - offset2;
        */

        gyro_rotation1 = (IMU1.GetGRotationZ()) - IMU1.GetGyroDrift();
        gyro_rotation2 = (IMU2.GetGRotationZ()) - IMU2.GetGyroDrift();
        acceleration_rotation1 = IMU1.GetRotation();
        acceleration_rotation2 = IMU2.GetRotation();

        finalAngle1 = KFilter1.Filter(gyro_rotation1, acceleration_rotation1);
        finalAngle2 = KFilter2.Filter(gyro_rotation2, acceleration_rotation2);

        
        angles.leg1_angle = finalAngle1;
        angles.leg2_angle = finalAngle2;

        chatter_pub.publish(angles);

        //printf("%f  , %f \n", gyro_rotation1, finalAngle1);

        ros::spinOnce();
        loop_rate.sleep();

    }

    return 0;
}

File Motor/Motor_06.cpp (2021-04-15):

#include "ros/ros.h"
#include "std_msgs/Int32.h"

#include <iostream>
#include <fstream>
#include <string>
#include <cstdlib>


class motor
{
    public:

    motor(int pinNumber)
    {
        m_dutyCycle = 1000000;
        setpwmPin (14);
        std::cout<< "Running with pin 14" << std::endl;
    }
    void setDutyCycle(int dutyC)
    {
        std::ofstream DCfile;
        DCfile.open("/sys/class/pwm/pwm-" + m_PinpathNumber + "/duty_cycle");
        DCfile << dutyC;
        DCfile.close();
    }
    void setPWMfreq(int frequency)
        {
            disablePWM();
            std::ofstream freqSet;
            freqSet.open("/sys/class/pwm/pwm-" + m_PinpathNumber + "/period");
            freqSet << frequency;
            freqSet.close();
            enablePWM();
        }

    void GPIOtoggle(int cape_nr,int pin_nr,int state)
    {   
        //intit addresses, states, and direction,
        setGPIOpin(cape_nr,pin_nr);
        setGPIOstate();
        //exportIOpin();
        setGPIOdirection("out");

        // Toggeling pin
        std::ofstream pinstream;
        pinstream.open("/sys/class/gpio/gpio"+ m_GPIONumber + "/value");
        pinstream << state;
        pinstream.close();
    }
    void toggleMotorPin(int state)
    {
          // Toggeling pin
        std::ofstream pinstream;
        std::ofstream pinstream2;

        pinstream.open("/sys/class/gpio/gpio115/value");
        pinstream << state;
        pinstream.close();
        pinstream2.open("/sys/class/gpio/gpio117/value");
        pinstream2 << state;
        pinstream2.close();

    }
    void motorInit()
    {   
        setPWMstate();
        exportPWM();
        setPWMfreq(m_frequency);
        setDutyCycle(m_dutyCycle);
        enablePWM();  
    }
    private:

        int m_frequency = 20000000;
        int m_dutyCycle;
        int m_PIN;
        int m_pinbool;
        std::string m_Pinpath;
        std::string m_PinpathNumber;
        std::string m_pinChip;

        std::string m_GPIONumber;
        std::string m_IOpinpath;

        void setGPIOpin(int cape_nr,int IO_pin) //change to return 1 if good, 0 bad.
        {
            switch (cape_nr)
            {
                case 9:
                    switch (IO_pin)  //not GPIO but pins from beaglebone cape
                    {
                     
                        case 25:
                        m_IOpinpath = "P9_25_pinmux";
                        m_GPIONumber = "117";
                        break;

                        case 27:
                        m_IOpinpath = "P9_27_pinmux";
                        m_GPIONumber = "115";
                        break;

                        default:
                        std::cout<<IO_pin << " is not an implemented pin"<< std::endl;
                        break;

                    }
                break;
              
                default:
                std::cout<<"pin : " <<cape_nr << " is an invalid cape_nr !" <<std::endl;
                break;
            }
        }
        void setGPIOstate()
        {
            std::ofstream IOstateStream;
            IOstateStream.open("sys/devices/platform/ocp/ocp:" + m_IOpinpath + "/state");
            IOstateStream << "default";
            IOstateStream.close();
        }
        void exportIOpin()
        {
            std::ofstream IOexportstream;
            IOexportstream.open("/sys/class/gpio/export");
            IOexportstream << m_GPIONumber;
            IOexportstream.close();
        }
        void setGPIOdirection(std::string direction)
        {
            std::ofstream IOdirStream;
            IOdirStream.open("/sys/class/gpio/gpio" + m_GPIONumber + "/direction");
            if (IOdirStream.fail())
            {
                exportIOpin();
                setGPIOdirection(direction);
                return;
            }
            IOdirStream << direction;
            IOdirStream.close();
        }


        void setpwmPin(int pin)
        {  
            switch (pin) 
            {
                case 14:
                    m_Pinpath = "P9_14_pinmux";
                    m_PinpathNumber = "4:0";
                    m_pinChip = "pwmchip4";
                    m_pinbool = 0;
                    break;
                case 16:
                    m_Pinpath = "P9_16_pinmux";
                    m_PinpathNumber = "4:1";
                    m_pinChip = "pwmchip4";
                    m_pinbool = 1;
                    break;
                default:
                    std::cout << "Not an implemented pin"<<std::endl;
                    break;
            }
        }
            
        void setPWMstate()
        {
            std::ofstream pwmstate;
            pwmstate.open("/sys/devices/platform/ocp/ocp:" + m_Pinpath + "/state");
            //få inn feiltest
            pwmstate << "pwm";
            pwmstate.close();
        }

        void enablePWM()
        {
            std::ofstream pwmEnable;
            pwmEnable.open("/sys/class/pwm/pwm-" + m_PinpathNumber + "/enable");
            pwmEnable << 1;
            pwmEnable.close();
        }
        void disablePWM()
        {
            std::ofstream pwmEnable;
            pwmEnable.open("/sys/class/pwm/pwm-" + m_PinpathNumber + "/enable");
            pwmEnable << 0;
            pwmEnable.close();
        }

        void exportPWM ()
        {
            std::ofstream PWMexportStream;
            PWMexportStream.open("/sys/class/pwm/" + m_pinChip + "/export");
            PWMexportStream << m_pinbool;
            PWMexportStream.close();
        }
        

};
motor control(29);

void chatterCallback(const std_msgs::Int32::ConstPtr& msg)
{
    //ros code
    ROS_INFO("servo_recive : %d", msg->data);
    int encoderPos = msg->data;

    //servo code

    if (encoderPos < 1000)
    {
        control.toggleMotorPin(0);  //set GPIO pin 25 on cape 9 to 0
        //control.GPIOtoggle(9,27,0);  //set GPIO pin 23 on cape 9 to 0   counterclockwise   
        //ROS_INFO("inside if : [%s]", encoderPos);
    }
    else
    {
        control.toggleMotorPin(1);
        //control.GPIOtoggle(9,25,1); //set GPIO pin 25 on cape 9 to 1
        //control.GPIOtoggle(9,27,1); //set GPIO pin 27 on cape 9 to 1    clockwise
       // ROS_INFO("outside if : [%s]", encoderPos);
    }
    
}


int main(int argc, char **argv)
{

    
    control.motorInit();
    control.setDutyCycle(8000000);  // 80%
    control.setPWMfreq(10000000);   //100Hz
    control.GPIOtoggle(9,27,1); // MOTOR OFF
    control.GPIOtoggle(9,25,0); // MOTOR OFF
    

    //ros code
    ros::init(argc, argv, "motor_subscriber");
    ros::NodeHandle n;
    ros::Subscriber sub = n.subscribe("chatter", 1000, chatterCallback);
    ros::spin();
    return 0;
}

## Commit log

2021-03-10 functioning IMUcode :)
2021-03-11 added PI regulator to offset
2021-03-11 wrote info about the IMU implementation
2021-03-17 IMU code changes
2021-03-17 motor subscriber package added
2021-03-25 added board design files
2021-03-25 signal voltage boost added to boards
2021-03-25 updated board viles
2021-04-12 Added ServoCasing CAD file
    [ServoCasing.stl]
2021-04-12 Added documentation folder
    [Arm.SLDPRT, Arm_10mm.SLDPRT, Assem1.SLDASM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]
2021-04-14 IMU and encoder working and using Float32MultiArray as message
2021-04-16 Add files via upload
    Uploaded pictures of the servo controller config.
2021-04-18 Update README.md
    Added readme of Configure the servo-controller
2021-04-22 New working encoder reading integration
2021-04-22 added rqt and rviz
    [body_link.stl, leg_01.stl, leg_02.stl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]
2021-04-23 new stuff
    [robot.urdf]
2021-04-24 new motor cpp file
2021-04-24 new imu loggin code adde for tubble shooting
2021-04-24 new motor code with pid added
2021-04-27 Add files via upload
    Picture of gearbox
2021-04-28 IMU update
2021-04-28 motor build
2021-04-28 Update Motor_08.cpp
    Commented toggleMotorPin
2021-05-03 IMU kalman filter implement
2021-05-03 motor messages updated
2021-05-03 new servo code
2021-05-04 Servo tweeks
2021-05-19 added board files
